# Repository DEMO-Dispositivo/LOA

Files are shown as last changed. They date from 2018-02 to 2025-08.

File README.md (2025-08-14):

# LOA
Robots for Lucifer's Ensemble LOA project.
Playing 3 drums made using Lavacolhos techniques inspired by the Arada drums and other percussions.
The boards are Arduino-based and can receive MIDI through DIN cable or play via SD Card.

## BOARDS

### Legba 
- Arduino MEGA
- 3 servos (5V)
- 7 solenoids (12V)
- 2 motors (5V or 12V)

### Damballah
- Arduino UNO
- 1 servo (5V)
- 3 solenoids (12V)
- 2 motors (5V or 12V)

### Samedi
- Arduino UNO
- 1 servo (5V)
- 3 solenoids (12V)
- 2 motors (5V or 12V)

## BOM
[BOM Spreadsheet](https://docs.google.com/spreadsheets/d/1H9ps_YcNi2U3gRdNnN2o0KlRJA077tAUcP5HMw0Rx48/edit?usp=sharing)

## SCHEMATICS
[Legba board](../master/schematics/Legba_schematic_rev1.pdf)

## MIDI Note Mapping
### Legba
- Note 0: solenoid 1
- Note 2: solenoid 2
- Note 4: solenoid 3
- Note 5: solenoid/motor 4
- Note 7: solenoid/motor 5
- Note/CC 9: servo 1
- Note 36: solenoid 6
- Note 38: solenoid 7 
- Note 40: solenoid 8
- Note/CC 43: servo 2
- Note/CC 45: servo 3

### Damballah
- Note 12: solenoid 1
- Note 14: solenoid 2
- Note 16: solenoid 3
- Note 17: solenoid/motor 4
- Note 19: solenoid/motor 5
- Note 21: servo 1

### Samedi
- Note 24: solenoid 1
- Note 26: solenoid 2
- Note 28: solenoid 3
- Note 29: solenoid/motor 4
- Note 31: solenoid/motor 5
- Note 33: servo 1

## Special thanks to
- Américo Simões
- Tiago Fróis
- Gil MAC and Cláudio Vidal
- FEUP (Faculty of Engineering - University of Porto)
- FCT (Foundation for Science and Technology)

[][cc-by-nc]

This work is licensed under a
[Creative Commons Attribution-NonCommercial 4.0 International License][cc-by-nc].

[][cc-by-nc]

[cc-by-nc]: https://creativecommons.org/licenses/by-nc/4.0/
[cc-by-nc-image]: https://licensebuttons.net/l/by-nc/4.0/88x31.png
[cc-by-nc-shield]: https://img.shields.io/badge/License-CC%20BY--NC%204.0-lightgrey.svg

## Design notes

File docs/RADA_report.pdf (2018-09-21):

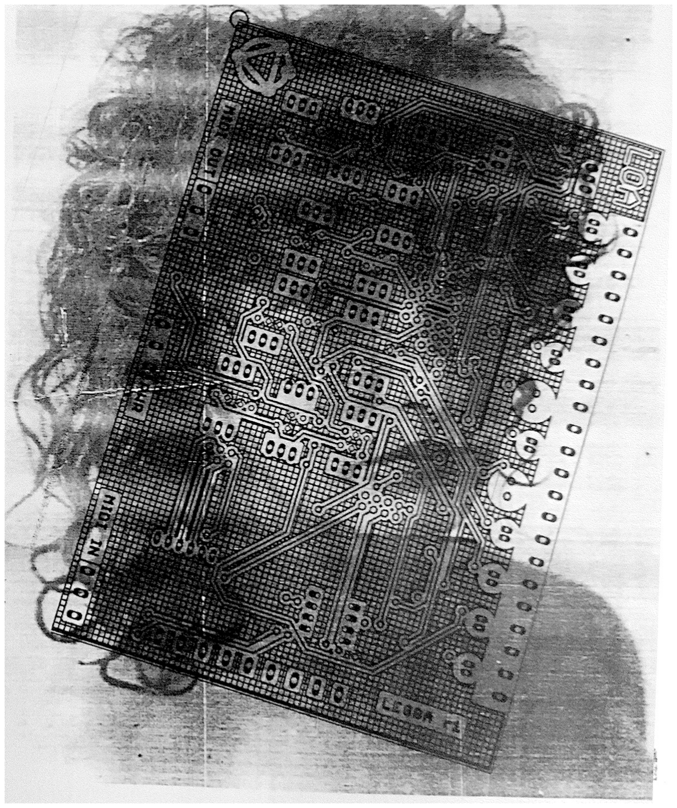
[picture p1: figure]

# RADA™

Tiago Ângelo
FEUP-PDMD
tiago.a.s.angelo@gmail.com
Rada™ | www.tiagoangelo.net

# RESUMO

RADA™ é um ensemble musical robó4co integrado no projecto LOA (https://barosamedi.tumblr.com) desenvolvido pelo colec4vo Lucifer’s Ensemble. (http://www.lucifersensemble.org) Loa é uma reflexão sobre o Vodu do Louisiana e especialmente do Hai4, estabelecendo pontes entre a arte, a antropologia, o experimental e o ancestral. Tendo como ponto de par4da os trabalhos da coreógrafa, bailarina, escritora e cineasta experimental Maya Deren, tais como Religious Possession in Dancing e Divine Horsemen: The Living Gods of Hai4.
Rada refere-se a um conjunto de Loas (divindades) e rituais descendentes do Reino Dahomey (actual República do Benin), cujas cerimónias fazem uso da percussão Rada - um ensemble cons4tuído por uma família de três tambores de madeira com membranas feitas de pele de vaca: o manman (o tambor maior), o segon (tambor médio) e o boula (tambor mais pequeno). Nestas cerimónias a função dos percussionistas é a de es4mular e interagir com a possessão dos par4cipantes, que se mostram ‘montados’ pelos Loas.
O Vodu, como religião ancestral, tem sofrido constantes mutações ao longo dos anos, exibindo diferentes artefactos e expressões culturais mistas espalhadas por diversos países como o Hai4, Benin, Togo, Cuba ou Brasil, para mencionar apenas alguns. Desta forma, o projecto RADA™ não pretende ser uma emulação robó4ca das percussões e percussionistas Rada, mas sim um ensemble robó4co único, inspirado nas suas percussões bem como nos padrões rítmicos usados nos seus vários ritos. Pretendendo explorar a relação entre a música e estados de transe, usando algoritmos de música genera4va para gerar performances de longa duração baseadas em transcrições de um conjunto de padrões musicais dedicados a certos Loas (ex: Legba ou Samedi), colocando a questão: serão os autómatos capazes de nos induzir em estados de transe ?

# ABSTRACT

RADA™ is a robo4c music ensemble integrated in the LOA (https://barosamedi.tumblr.com) project developed by the Lucifer’s Ensemble collec4ve. LOA is a reflec4on over Hai4an and Louisiana Voodoo, bridging art, anthropology, (http://www.lucifersensemble.org) the experimental and the ancestral. The star4ng point of research begins with the works of the choreographer, dancer, writer and experimental filmmaker Maya Deren, such as the Religious Possession in Dancing and Divine Horsemen: The Living Gods of Hai4.
Rada is a set of Loas (dei4es) and rites that descend from the Kingdom of Dahomey (presently Republic of Benin), using in its cerimonies the Rada bacery - an ensemble comprised of a family of three drums made out of carved wood and a membrane made of cowhide: the manman (the biggest drum), segon (medium drum) and boula (smallest drum). Where the drummers role in such rites is to both s4mulate and interact with the possession of the par4cipants, said to be ‘mounted’ by the Loas.
Voodoo, as an ancestral religion, has been under constant muta4on over the ages, exhibi4ng different artefacts and mixed cultural expressions spread around several countries such as Hai4, Benin, Togo, Cuba or Brasil, just to name a few. Likewise, RADA™ is not a robo4c emula4on of the Rada bacery and percussionists but rather a unique robo4c ensemble inspired by Rada drums and the rhythmic pacerns used in its rites. It aims to explore the rela4onship between music and trance states, using genera4ve music algorithms to generate long dura4on performances based on transcrip4ons of a set of musical pacerns dedicated to given Loas (such as Legba or Samedi), posing the ques4on: can automatons induce us into trance-like states ?

# DESCRIÇÃO TÉCNICA

## Instrumentos e actuadores

O ensemble RADA™ é cons4tuído por três tambores construídos por Américo Simões usando as técnicas empregues nos bombos de Lavacolhos (Fundão, Portugal), cujo corpo do instrumento é feito de metal com um aro em madeira, membrana de pele de cabra e corda para es4car/afinar a pele. As dimensões dos tambores são de 50x50cm, 40x40cm e 30x30cm. Para cada tambor existe um controlador responsável por traduzir mensagens MIDI em impulsos eléctricos enviados para os actuadores, sendo que em cada tambor existem:
- 2 motores DC com fitas de tecido que percutem a membrana criando padrões polirrítmicos semi-aleatórios de acordo com a sua velocidade de rotação;
- 3 solenóides com pontas de baqueta construídas para o propósito, percu4ndo a membrana, o aro de madeira e o corpo metálico, respec4vamente;
- 1 servo acoplado a um mecanismo ad hoc que tem a função de pressionar a membrana, criando alterações de tom quando o solenóide percute a membrana.

Os tambores estão suspensos do chão por um suporte em metal desenhado para o propósito, para o qual foram desenhados suportes em madeira que sustentam e posicionam os actuadores de modo a percu4rem os instrumentos.
Adicionalmente poderão exis4r 4 solenóides extra para percu4r vários objectos, à imagem do ogan
- sino usado na percussão Rada - e que de acordo com registos etnográficos poderão ser usados, além de um sino de metal, pedras, garrafas de vidro ou pedaços de espadas de material metálico. Bem como 2 motores servo para cumprir a função do ason (maraca). Estes controlos fazem parte do controlador LEGBA, correspondente ao tambor maior.

## Controladores e configuração

De modo a controlar todos os actuadores existem 3 caixas (LEGBA, DAMBALLAH e SAMEDI) contendo um Arduino¹, uma fonte de alimentação comutada de 12V, uma fonte de alimentação comutada de 5V, uma PCB 4po shield de Arduino para controlo dos actuadores bem como envio e recepção de mensagens MIDI. Cada caixa inclui ligações de corrente eléctrica com conector Speakon, entrada e saída MIDI via XLR, entrada DC para alimentação do Arduino, porta USB para programação, saídas DC para conexão de motores e solenóides e saídas Jack stereo 6.3mm para conexão dos servos.
O controlo do autómato (ver figura em baixo) é realizado através de um computador ligado a uma interface MIDI que por sua vez se liga ao controlador LEGBA usando um cabo conversor de MIDI DIN (5 pinos a 180°) para XLR, que por sua vez transmite as mensagens MIDI através de cabos XLR ligados em série aos restantes controladores.

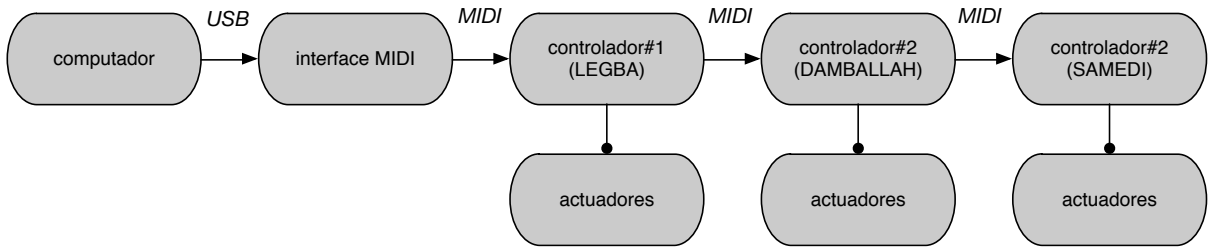
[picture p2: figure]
computador; interface MIDI; controlador#1; (LEGBA); controlador#2 (DAMBALLAH); controlador#2 (SAMEDI); actuadores; USB; MIDI

1 www.arduino.cc

## Composição generaDva em tempo-real

O algoritmo responsável pela execução do autómato é cons4tuído por três fases dis4ntas (ver fig. em baixo):
1. Transcrição e colecção: numa primeira fase será feita uma transcrição manual de vários registos² em formato áudio ou par4tura de música tradicional do Hai4, procedendo-se a uma codificação para um formato próprio para o posterior algoritmo gené4co e gravação destes ficheiros codificados numa base de dados;
2. Nesta fase proceder-se-á à geração de vários ficheiros codificados de modo a treinar uma rede neuronal supervisionada de modo a que na fase seguinte a função de fitness (fitness func6on) seja automá4ca (sem supervisão), escolhendo as ‘melhores’ gerações de padrões musicais.
3. A úl4ma fase será a que ficará em funcionamento durante a instalação, sendo que o algoritmo irá correr de modo conxnuo desde o início ao final do fes4val Semibreve (mesmo que se reinicie o sistema diariamente). Nesta fase o algoritmo irá inicialmente começar a gerar padrões musicais recorrendo à base de dados inicial (ficheiros codificados de música tradicional hai4ana) sendo a piscina gené4ca (gene6c pool) retro-alimentada com novas gerações que passem no função de fitness. Este processo fará com que inicialmente a instalação comece com padrões musicais com elevado grau de semelhança em relação às transcrições iniciais e caminhe progressivamente para o ‘desconhecido’, isto é, poderá terminar com padrões musicais completamente diferentes dos iniciais, sendo introduzidas ligeiras mutações gené4cas nos padrões a cada iteração.

Base de
dados
inicial

Partituras ou
gravações áudio

Ficheiro
codificado

Transcrição
manual | Codificação

### Fase 1: transcrição e colecção

### Fase 2: treino

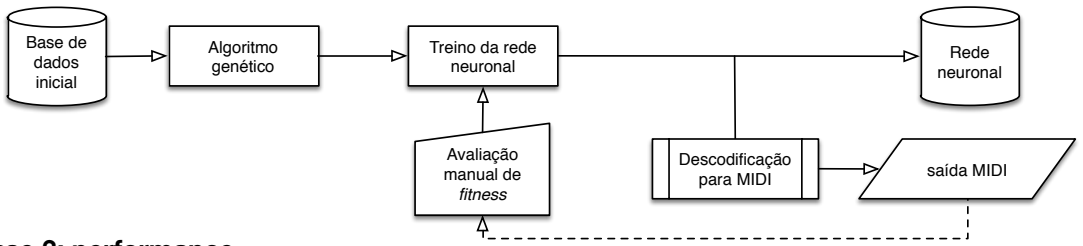
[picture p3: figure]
Rede neuronal; Base de dados inicial; Algoritmo genético; Treino da rede neuronal; Avaliação manual de fitness; saída MIDI Descodificação para MIDI

### Fase 3: performance

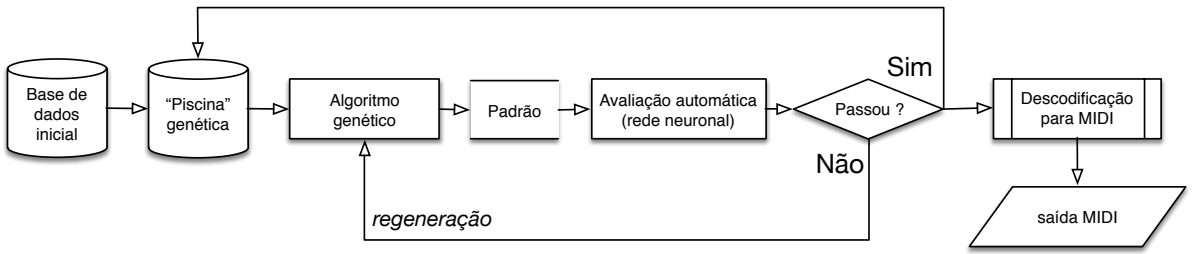
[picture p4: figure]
“Piscina” genética; Base de dados inicial; Algoritmo genético; Avaliação automática; (rede neuronal) Padrão; Passou ?; Sim; Não; regeneração; Descodificação para MIDI; saída MIDI

2 Fontes principais: “The Drum and the Hoe: Life and Lore of the Hai4an People” (Harold Courlander, 1960); “Voodoo Trance Music Ritual Drums of Hai4” (Lyrichord edi4on, 1974); “Divine Horsemen - The Voodoo Gods of Hai4” (recorded by Maya Deren, 1947-51, Lyrichord edi4on)

# PLANO DE MONTAGEM

1. Colocação das bases metálicas
2. Colocação dos tambores nas bases metálicas
3. Colocação dos suportes de madeira
4. Colocação do suporte lateral de acordo com a marcação (LEGBA no tambor grande, DAMBALLAH no médio e SAMEDI no pequeno)
5. Colocação das caixas ao lado de cada tambor: caixa LEGBA com o tambor maior, caixa DAMBALLAH com o tambor médio, caixa SAMEDI com o tambor pequeno
6. Ligação dos cabos dos actuadores de cada tambor à respec4va caixa de acordo com a enumeração marcada no cabo e na caixa
7. Ligação dos 2 cabos XLR (LEGBA MIDI OUT —> DAMBALLAH MIDI IN e DAMBALLAH MIDI OUT —> Samedi MIDI IN)
8. Ligação de corrente: 3 cabos Speakon e 3 adaptadores 12V DC providenciados
9. Ligação da interface MIDI ao computador conectando o cabo conversor (DIN-XLR) ao MIDI OUTPUT da interface, usando um cabo XLR rela4vamente comprido para fazer a conexão entre o cabo conversor e a caixa LEGBA na ficha MIDI IN
10. Ligar o computador (que deverá arrancar automa4camente o programa RADA). Pressionar a tecla ’T’ do teclado do computador para testar e pressionar a tecla ‘ENTER’ para começar. No caso de engano poder-se-á pressionar a tecla ‘C’ para restabelecer o programa ao estado inicial, pressionando novamente a tecla ‘ENTER’ para começar.
11. Depois poder-se-á desconectar o teclado do computador e guardar, ficando apenas o monitor visível para efeitos de visualização da geração de padrões musicais.
12. Colocação de pufes ou lugares sentados para escuta.

Duração prevista de montagem: 4h; 2 pessoas; material necessário: chave inglesa e alicate de pontas.

## Disposição:

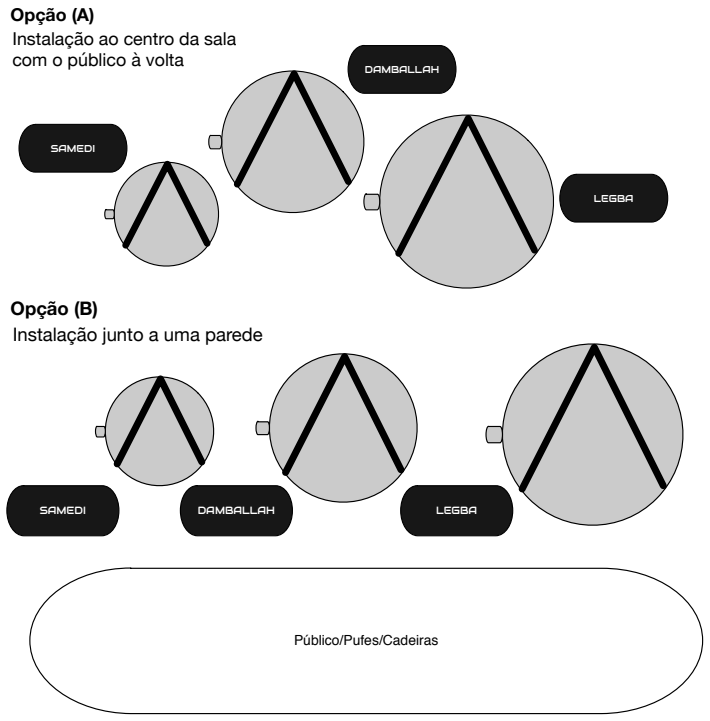
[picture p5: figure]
Opção (A); LEGBA; DAMBALLAH; SAMEDI; Instalação ao centro da sala com o público à volta; Opção (B); Instalação junto a uma parede; Público/Pufes/Cadeiras

## Raider:

1. Computador
2. Extensão de corrente eléctrica para 12 tomadas
3. [OPCIONAL] PA, mesa de mistura e 3 microfones com tripé de chão para amplificação dos tambores, dependendo da localização da instalação e acús4ca da sala (a combinar com o autor)

## Notas:

- O computador deverá ser programado para iniciar e terminar automa4camente para poder gravar a piscina gené4ca automa4camente de modo a poder con4nuar do mesmo sí4o no dia seguinte. Para tal é necessário que haja corrente eléctrica a uma determinada hora (a combinar com a ins4tuição de acolhimento) e que se desligue apenas depois do computador se ter desligado automa4camente. Para tal terá que se instalar um script no computador.
- O computador poderá ter sistema opera4vo Windows ou OSX. A versão é indiferente desde que conhecida previamente para efeitos de testes, embora seja preferido o sistema opera4vo OSX entre 10.9 e 10.11. A interface MIDI poderá no entanto ser providenciada pelo autor.

# Créditos

Tiago Ângelo - conceito, electrónica, programação e composição. Tiago Fróis - desenho e construção de suportes mecânicos. Américo Simões - construção dos tambores.

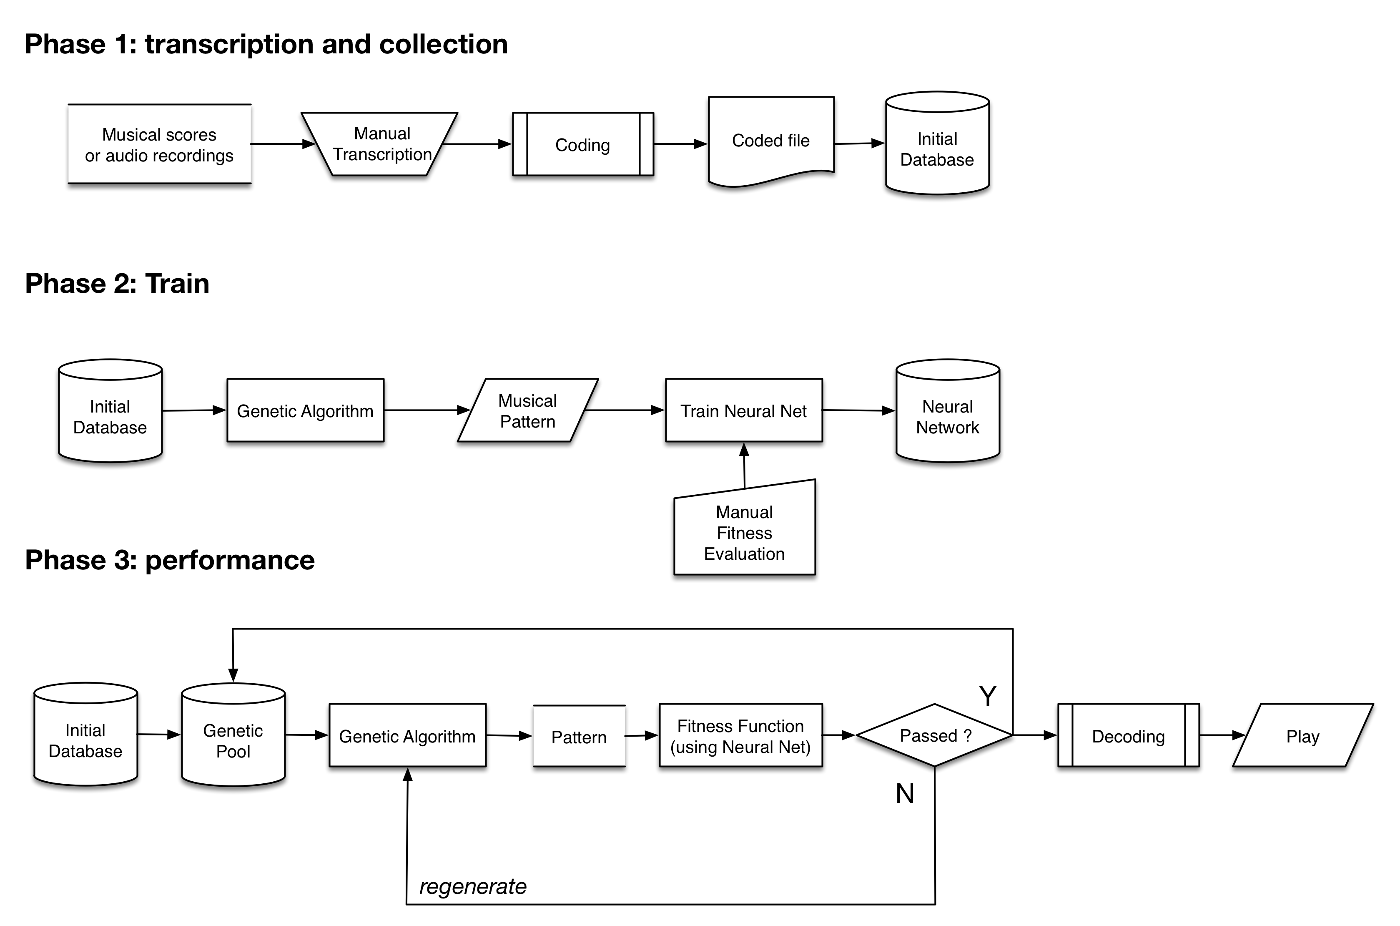
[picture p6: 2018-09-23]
MaxMSP/media/general_diagram.png

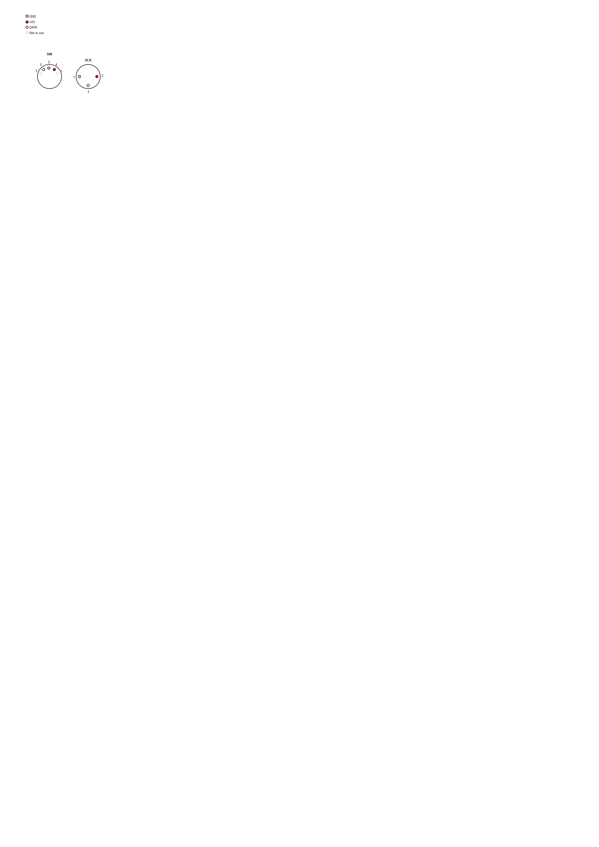
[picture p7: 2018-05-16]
docs/DIN to XLR.png

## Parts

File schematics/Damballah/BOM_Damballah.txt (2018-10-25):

Partlist exported from C:/Users/tiago/Documents/GitHub/LOA/schematics/Damballah/LOA_Damballah.sch at 25-09-2018 17:31

Qty Value               Device              Package            Parts                                                 Description                          
1                       FE06W               FE06W              SV1                                                   FEMALE HEADER                        
11                      W237-102            W237-102           L1, L2, L3, L4, L5, L6, L7, L8, L9, M4, M5            WAGO SCREW CLAMP                     
6                       W237-103            W237-103           MIDI_IN, MIDI_OUT, PWRIN, S1, S2, S3                  WAGO SCREW CLAMP                     
11  0.1uF               CNP-C025-050X025    C025-050X025       C13, C15, C17, C19, C21, C23, C25, C27, C29, C31, C33 NON-POLARIZED CAP                    
11  0.22uF              CNP-C025-050X025    C025-050X025       C12, C14, C16, C18, C20, C22, C24, C26, C28, C30, C32 NON-POLARIZED CAP                    
9   100uF               CPOL-USE3.5-8       E3,5-8             C1, C2, C3, C4, C5, C6, C7, C8, C9                    POLARIZED CAPACITOR, American symbol 
11  1A/50V/1.1V         DIODE-KIT2          DIODE-1N4001-KIT   D1, D2, D3, D4, D5, D6, D7, D8, D9, D10, D11          Diode                                
11  1k                  1KOHM-VERT-1/4W-1%  AXIAL-0.1          R1, R2, R3, R4, R5, R6, R7, R8, R9, R10, R11          1kO resistor                         
1   200mA/100V/1V       DIODE-1N4148        DIODE-1N4148       D12                                                   Diode                                
3   220                 1KOHM-HORIZ-1/4W-5% AXIAL-0.3          R12, R13, R15                                         1kO resistor                         
2   220uF               CP-E-035X080        E-035X080          C10, C11                                              POLARIZED CAP                        
1   4K7                 1KOHM-HORIZ-1/4W-5% AXIAL-0.3          R14                                                   1kO resistor                         
1   6N138               6N138               DIL08              OK1                                                   MOTOROLA OPTO COUPLER                
2   7806                78XXS               78XXS              IC10, IC11                                            VOLTAGE REGULATOR                    
9   7815                78XXS               78XXS              IC1, IC2, IC3, IC4, IC5, IC6, IC7, IC8, IC9           VOLTAGE REGULATOR                    
1   ARDUINO_MEGA_R3FULL ARDUINO_MEGA_R3FULL ARDUINO_MEGA       B1                                                    Arduino Mega R3                      
2   IRF510              IRF520              TO220BV            Q10, Q11                                              HEXFET Power MOSFET                  
9   TIP120              ROCKETFARM_TIP120V  ROCKETFARM_TO220AV Q1, Q2, Q3, Q4, Q5, Q6, Q7, Q8, Q9                    NPN DARLINGTON TRANSISTOR

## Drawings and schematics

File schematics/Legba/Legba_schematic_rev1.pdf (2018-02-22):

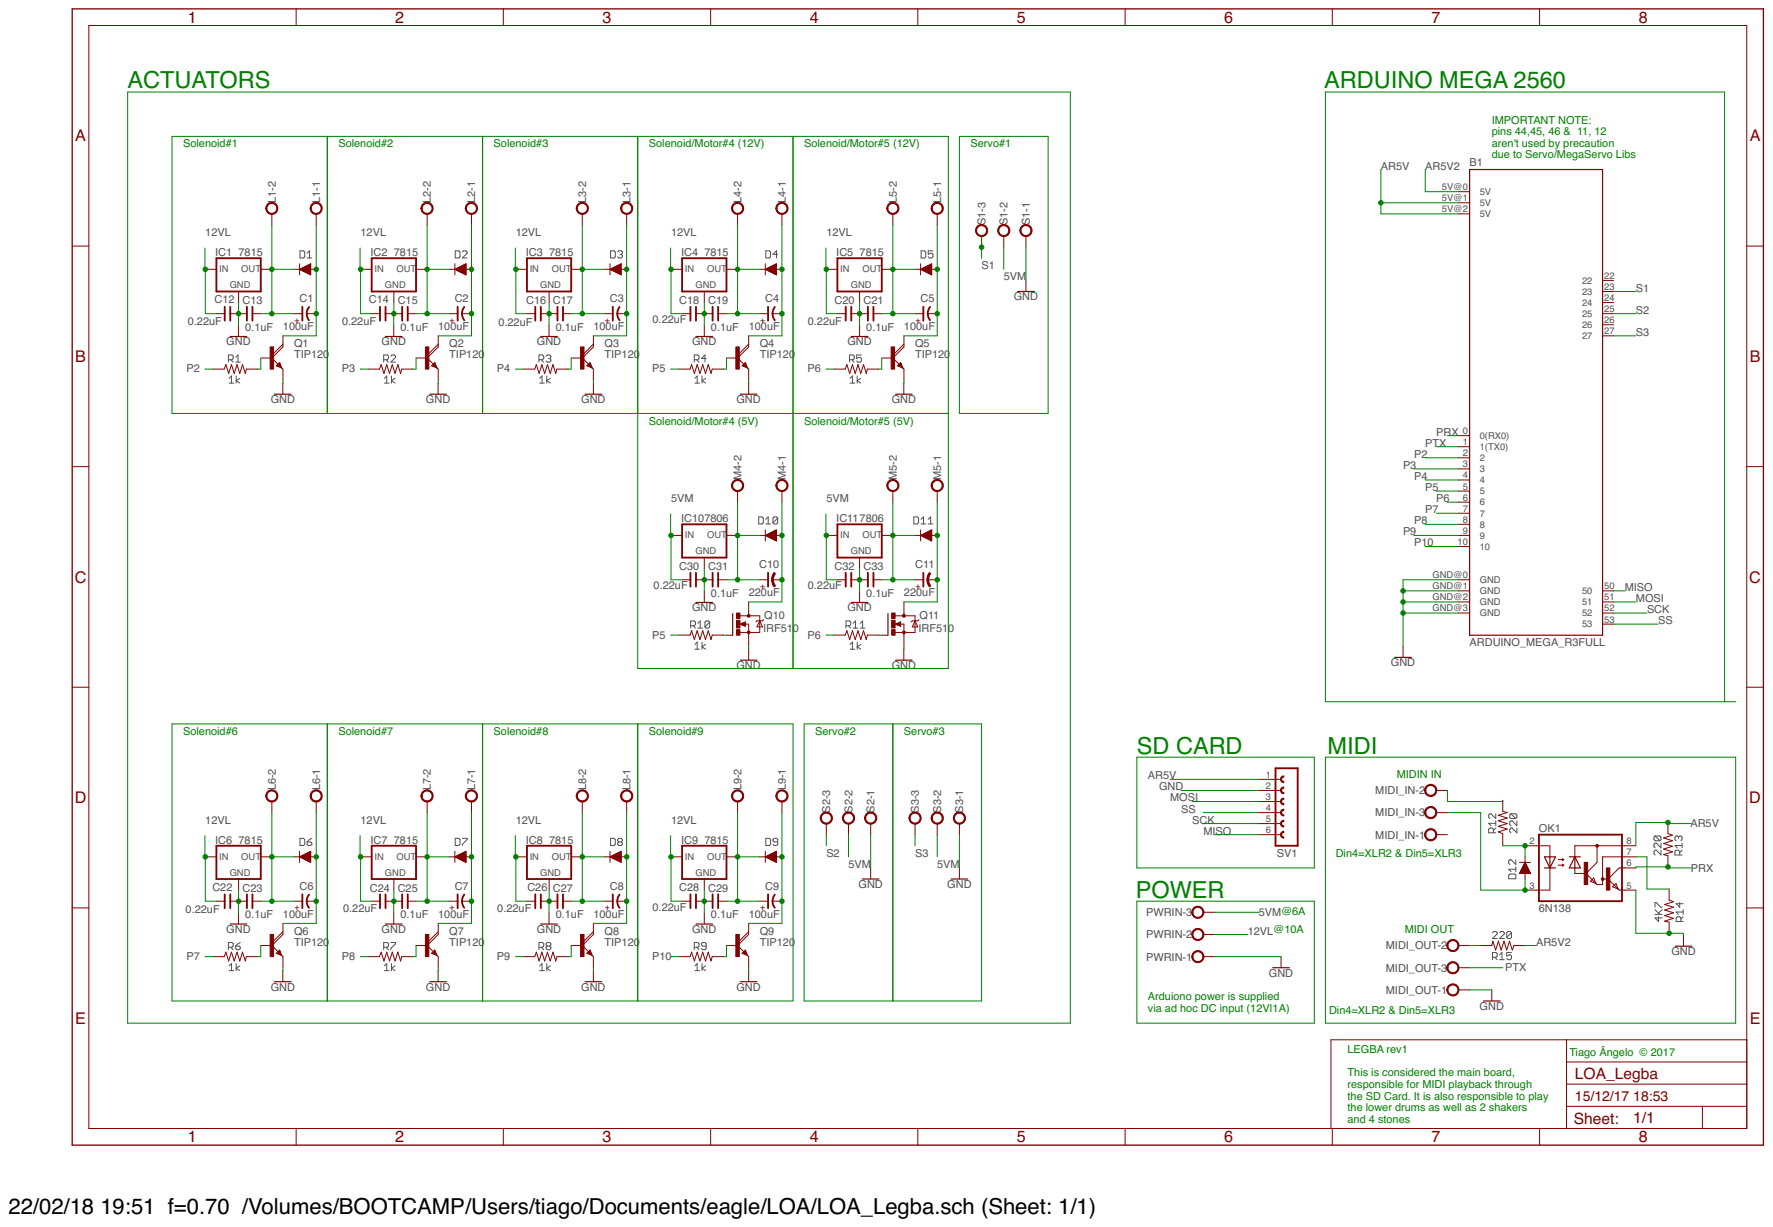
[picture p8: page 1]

aren't used by precaution

PWRIN-1 PWRIN-2 PWRIN-3 5VM @10A @6A 12VL Arduiono power is supplied via ad hoc DC input (12V|1A)

MIDI_OUT-1 MIDI_OUT-2 MIDI_OUT-3

LEGBA rev1 This is considered the main board, responsible for MIDI playback through

the SD Card. It is also responsible to play
the lower drums as well as 2 shakers and 4 stones

22/02/18 19:51 f=0.70 /Volumes/BOOTCAMP/Users/tiago/Documents/eagle/LOA/LOA_Legba.sch (Sheet: 1/1)

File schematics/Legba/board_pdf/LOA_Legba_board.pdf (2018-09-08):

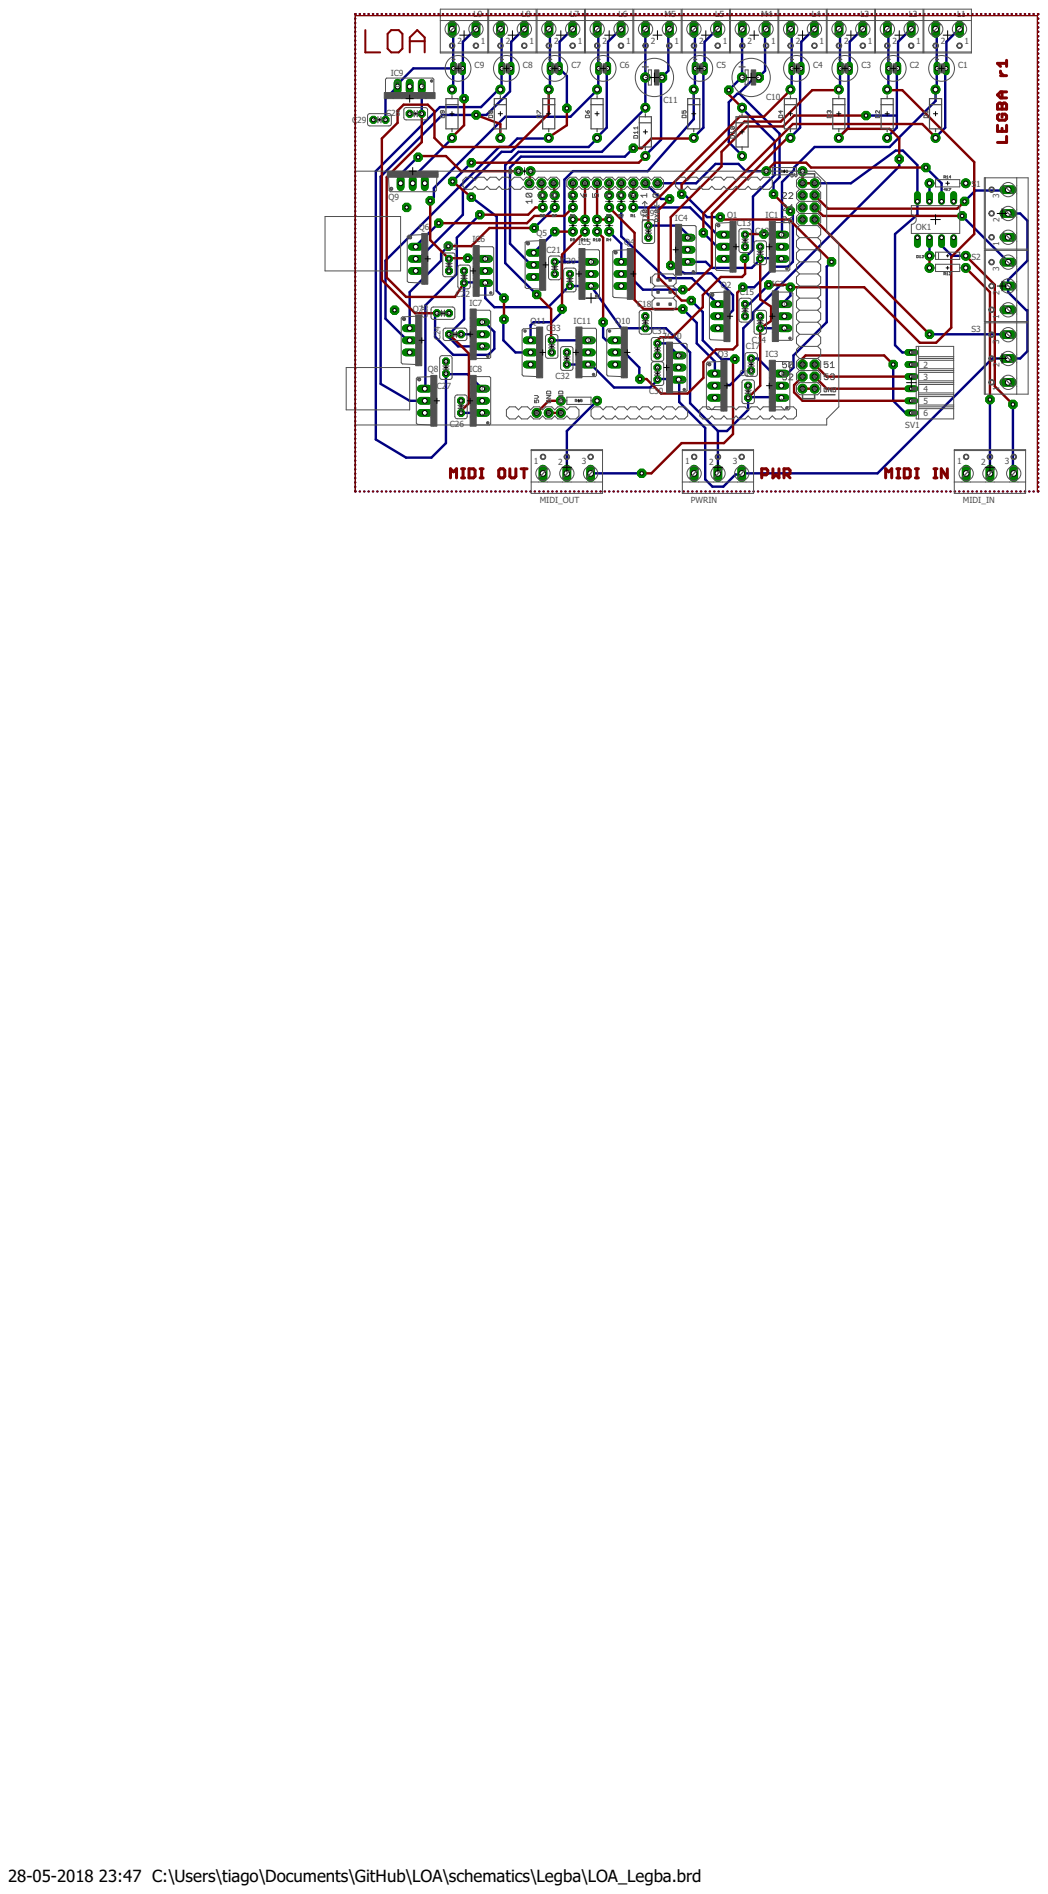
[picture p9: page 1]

28-05-2018 23:47 C:\Users\tiago\Documents\GitHub\LOA\schematics\Legba\LOA_Legba.brd

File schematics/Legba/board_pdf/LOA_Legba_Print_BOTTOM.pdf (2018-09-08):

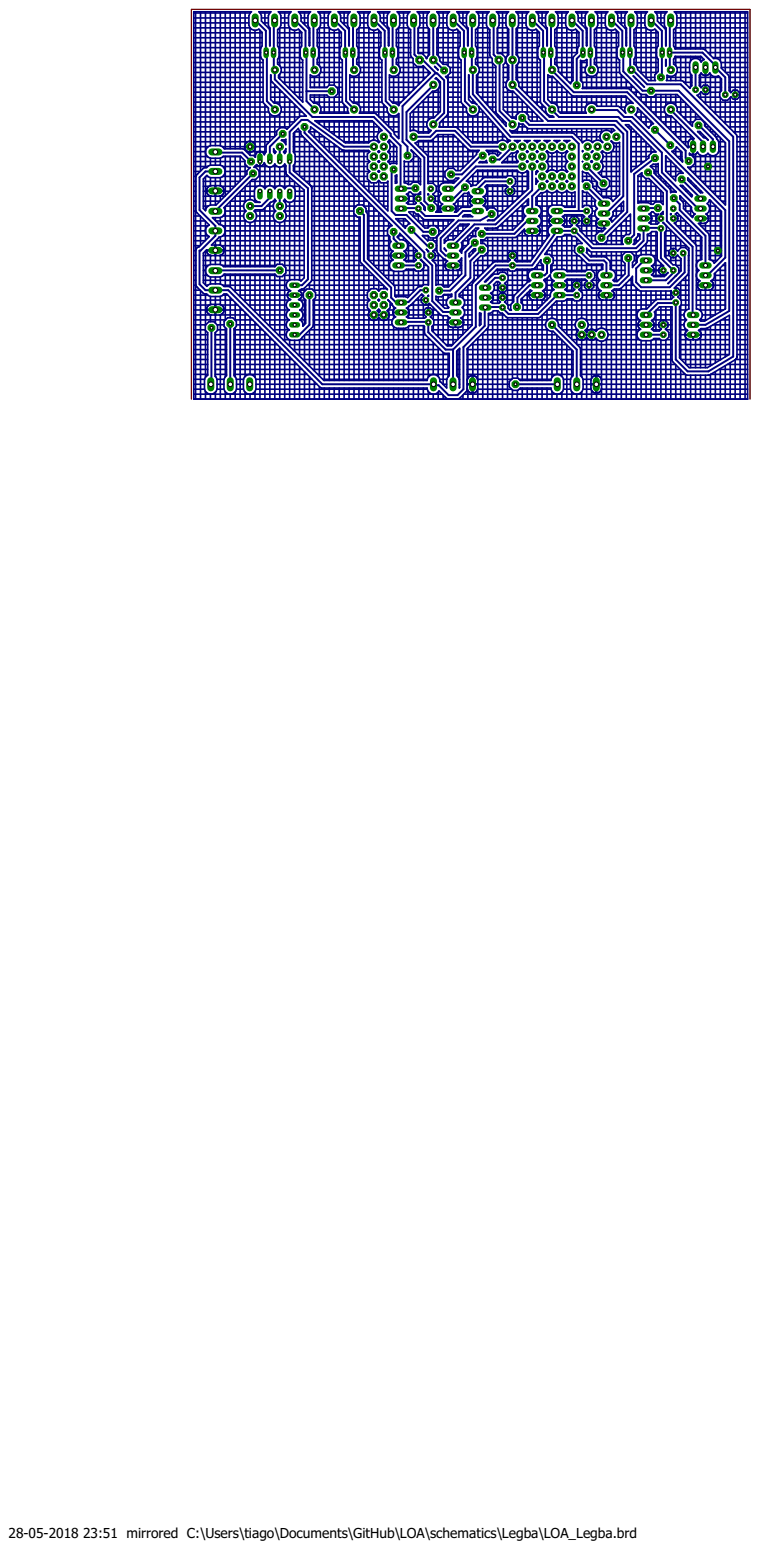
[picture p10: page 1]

28-05-2018 23:51 mirrored C:\Users\tiago\Documents\GitHub\LOA\schematics\Legba\LOA_Legba.brd

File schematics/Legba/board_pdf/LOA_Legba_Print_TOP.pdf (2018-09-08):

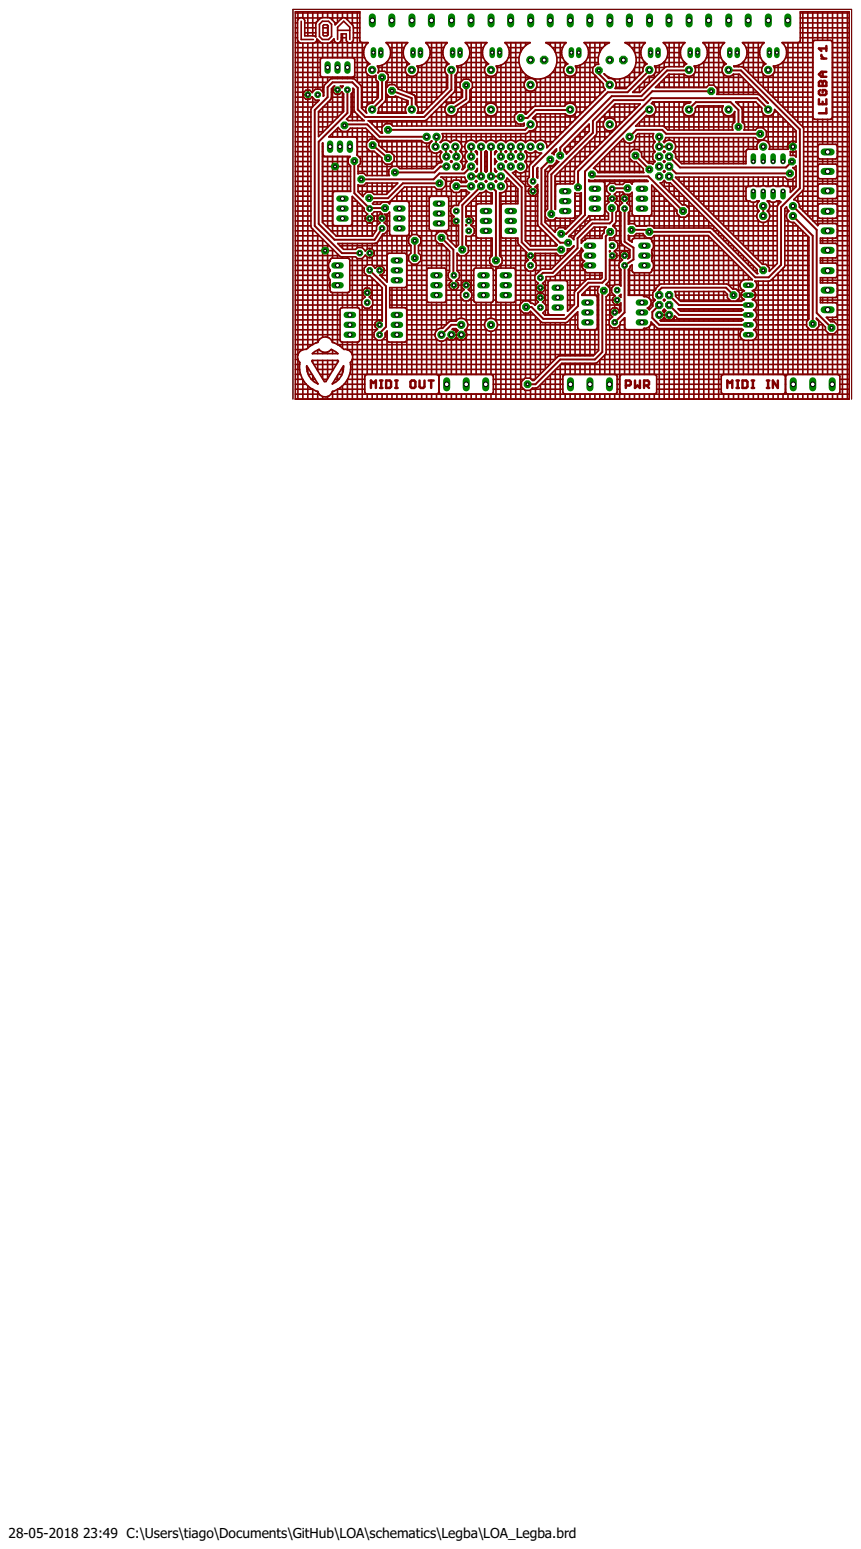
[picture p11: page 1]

28-05-2018 23:49 C:\Users\tiago\Documents\GitHub\LOA\schematics\Legba\LOA_Legba.brd

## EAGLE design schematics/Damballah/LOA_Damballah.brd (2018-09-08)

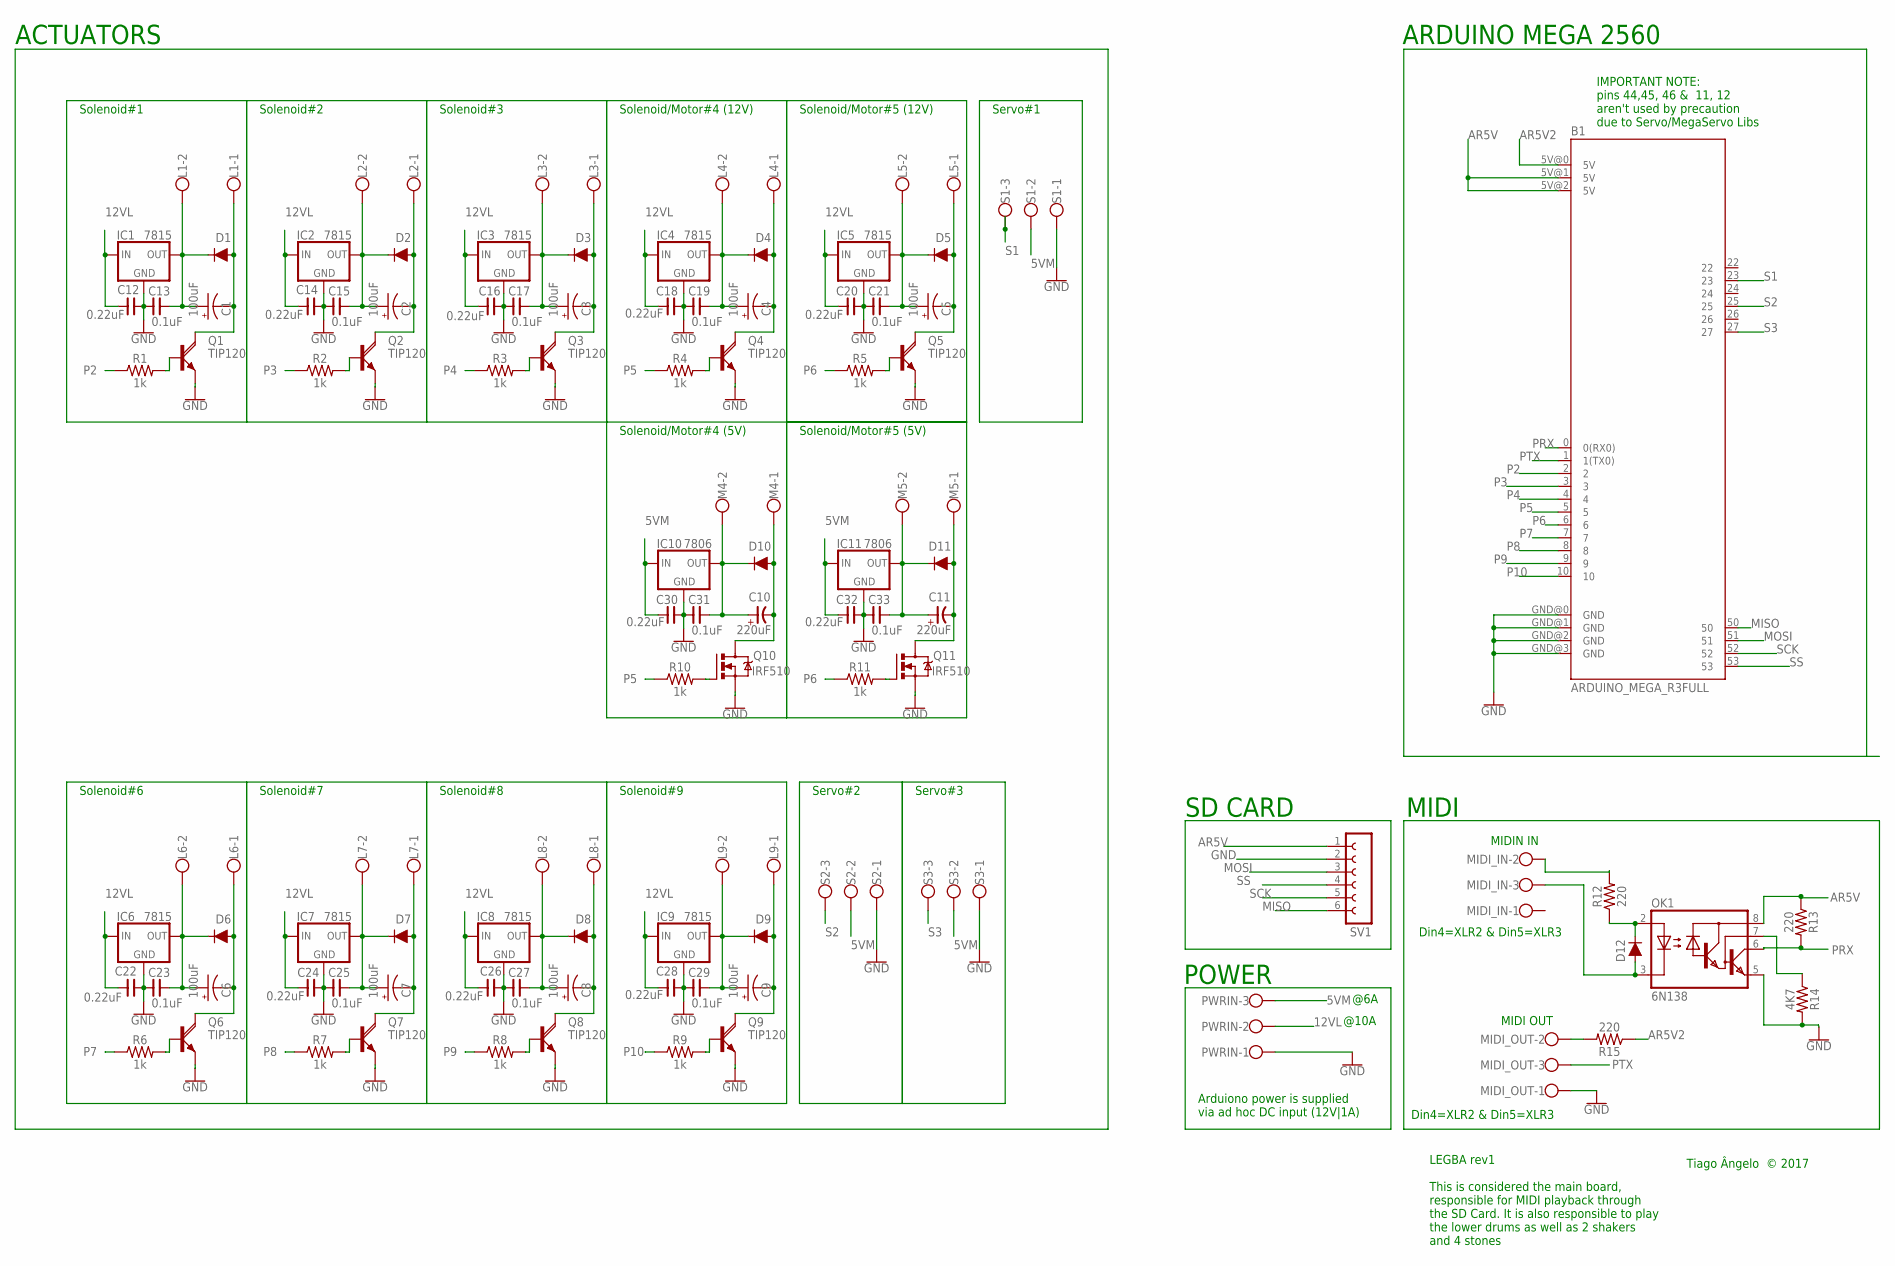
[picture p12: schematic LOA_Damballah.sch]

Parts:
B1: ARDUINO_MEGA_R3FULL; ARDUINO_MEGA
C1, C2, C3, C4, C5, C6, C7, C8, C9: 100uF; E3,5-8
C10, C11: 220uF; E-035X080
C12, C14, C16, C18, C20, C22, C24, C26, C28, C30, C32: 0.22uF; C025-050X025
C13, C15, C17, C19, C21, C23, C25, C27, C29, C31, C33: 0.1uF; C025-050X025
D1, D2, D3, D4, D5, D6, D7, D8, D9, D10, D11: 1A/50V/1.1V; DIODE-1N4001-KIT
D12: 200mA/100V/1V; DIODE-1N4148
IC1, IC2, IC3, IC4, IC5, IC6, IC7, IC8, IC9: 7815; 78XXS
IC10, IC11: 7806; 78XXS
L1, L2, L3, L4, L5, L6, L7, L8, L9: W237-102
M4, M5: W237-102
MIDI_IN: W237-103
MIDI_OUT: W237-103
OK1: 6N138; DIL08
PWRIN: W237-103
Q1, Q2, Q3, Q4, Q5, Q6, Q7, Q8, Q9: TIP120; ROCKETFARM_TO220AV
Q10, Q11: IRF510; TO220BV
R1, R2, R3, R4, R5, R6, R7, R8, R9, R10, R11: 1k; AXIAL-0.1
R12, R13, R15: 220; AXIAL-0.3
R14: 4K7; AXIAL-0.3
S1, S2, S3: W237-103
SV1: FE06W

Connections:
5VM: C30.1, C32.1, IC10.IN, IC11.IN, PWRIN.3, S1.2, S2.2, S3.2
12VL: C12.1, C14.1, C16.1, C18.1, C20.1, C22.1, C24.1, C26.1, C28.1, IC1.IN, IC2.IN, IC3.IN, IC4.IN, IC5.IN, IC6.IN, IC7.IN, IC8.IN, IC9.IN, PWRIN.2
AR5V: B1.5V@1 (5V), B1.5V@2 (5V), OK1.8 (VCC), R13.P$1 (1), SV1.1
AR5V2: B1.5V@0 (5V), R15.P$1 (1)
GND: B1.GND@0 (GND), B1.GND@1 (GND), B1.GND@2 (GND), B1.GND@3 (GND), C12.2, C13.1, C14.2, C15.1, C16.2, C17.1, C18.2, C19.1, C20.2, C21.1, C22.2, C23.1, C24.2, C25.1, C26.2, C27.1, C28.2, C29.1, C30.2, C31.1, C32.2, C33.1, IC1.GND, IC2.GND, IC3.GND, IC4.GND, IC5.GND, IC6.GND, IC7.GND, IC8.GND, IC9.GND, IC10.GND, IC11.GND, MIDI_OUT.1, OK1.5 (GND), PWRIN.1, Q1.E, Q2.E, Q3.E, Q4.E, Q5.E, Q6.E, Q7.E, Q8.E, Q9.E, Q10.S, Q11.S, R14.P$2 (2), S1.1, S2.1, S3.1, SV1.2
L1-1: C1.-, D1.A, L1.1, Q1.C
L1-2: C1.+, C13.2, D1.C, IC1.OUT, L1.2
L2-1: C2.-, D2.A, L2.1, Q2.C
L2-2: C2.+, C15.2, D2.C, IC2.OUT, L2.2
L3-1: C3.-, D3.A, L3.1, Q3.C
L3-2: C3.+, C17.2, D3.C, IC3.OUT, L3.2
L4-1: C4.-, D4.A, L4.1, Q4.C
L4-2: C4.+, C19.2, D4.C, IC4.OUT, L4.2
L5-1: C5.-, D5.A, L5.1, Q5.C
L5-2: C5.+, C21.2, D5.C, IC5.OUT, L5.2
L6-1: C6.-, D6.A, L6.1, Q6.C
L6-2: C6.+, C23.2, D6.C, IC6.OUT, L6.2
L7-1: C7.-, D7.A, L7.1, Q7.C
L7-2: C7.+, C25.2, D7.C, IC7.OUT, L7.2
L8-1: C8.-, D8.A, L8.1, Q8.C
L8-2: C8.+, C27.2, D8.C, IC8.OUT, L8.2
L9-1: C9.-, D9.A, L9.1, Q9.C
L9-2: C9.+, C29.2, D9.C, IC9.OUT, L9.2
M4-1: C10.-, D10.A, M4.1, Q10.D
M4-2: C10.+, C31.2, D10.C, IC10.OUT, M4.2
M5-1: C11.-, D11.A, M5.1, Q11.D
M5-2: C11.+, C33.2, D11.C, IC11.OUT, M5.2
MISO: B1.50, SV1.6
MOSI: B1.51, SV1.3
unnamed: Q10.G, R10.P$2 (2)
unnamed: MIDI_OUT.2, R15.P$2 (2)
unnamed: Q2.B, R2.P$2 (2)
unnamed: Q3.B, R3.P$2 (2)
unnamed: Q4.B, R4.P$2 (2)
unnamed: Q5.B, R5.P$2 (2)
unnamed: Q11.G, R11.P$2 (2)
unnamed: Q6.B, R6.P$2 (2)
unnamed: Q7.B, R7.P$2 (2)
unnamed: Q8.B, R8.P$2 (2)
unnamed: Q1.B, R1.P$2 (2)
unnamed: Q9.B, R9.P$2 (2)
unnamed: D12.A, MIDI_IN.3, OK1.3 (C)
unnamed: D12.C, OK1.2 (A), R12.P$1 (1)
unnamed: MIDI_IN.2, R12.P$2 (2)
unnamed: OK1.7 (VB), R14.P$1 (1)
P2: B1.2, R1.P$1 (1)
P3: B1.3, R2.P$1 (1)
P4: B1.4, R3.P$1 (1)
P5: B1.5, R4.P$1 (1), R10.P$1 (1)
P6: B1.6, R5.P$1 (1), R11.P$1 (1)
P7: B1.7, R6.P$1 (1)
P8: B1.8, R7.P$1 (1)
P9: B1.9, R8.P$1 (1)
P10: B1.10, R9.P$1 (1)
PRX: B1.0 (0(RX0)), OK1.6 (VO), R13.P$2 (2)
PTX: B1.1 (1(TX0)), MIDI_OUT.3
S1: B1.23, S1.3
S2: B1.25, S2.3
S3: B1.27, S3.3
SCK: B1.52, SV1.5
SS: B1.53, SV1.4

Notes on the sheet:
Tiago Ângelo © 2017
Din4=XLR2 & Din5=XLR3
MIDI OUT
MIDIN IN
MIDI
POWER
Arduiono power is supplied via ad hoc DC input (12V|1A)
IMPORTANT NOTE: pins 44,45, 46 & 11, 12 aren't used by precaution due to Servo/MegaServo Libs
Solenoid#1
Solenoid#2
Solenoid#3
Servo#1
Solenoid/Motor#4 (5V)
Solenoid/Motor#5 (5V)
Solenoid/Motor#4 (12V)
Solenoid/Motor#5 (12V)
Servo#2
Servo#3
Solenoid#6
Solenoid#7
Solenoid#8
Solenoid#9
SD CARD
ARDUINO MEGA 2560
ACTUATORS
@10A
@6A
LEGBA rev1 This is considered the main board, responsible for MIDI playback through the SD Card. It is also responsible to play the lower drums as well as 2 shakers and 4 stones

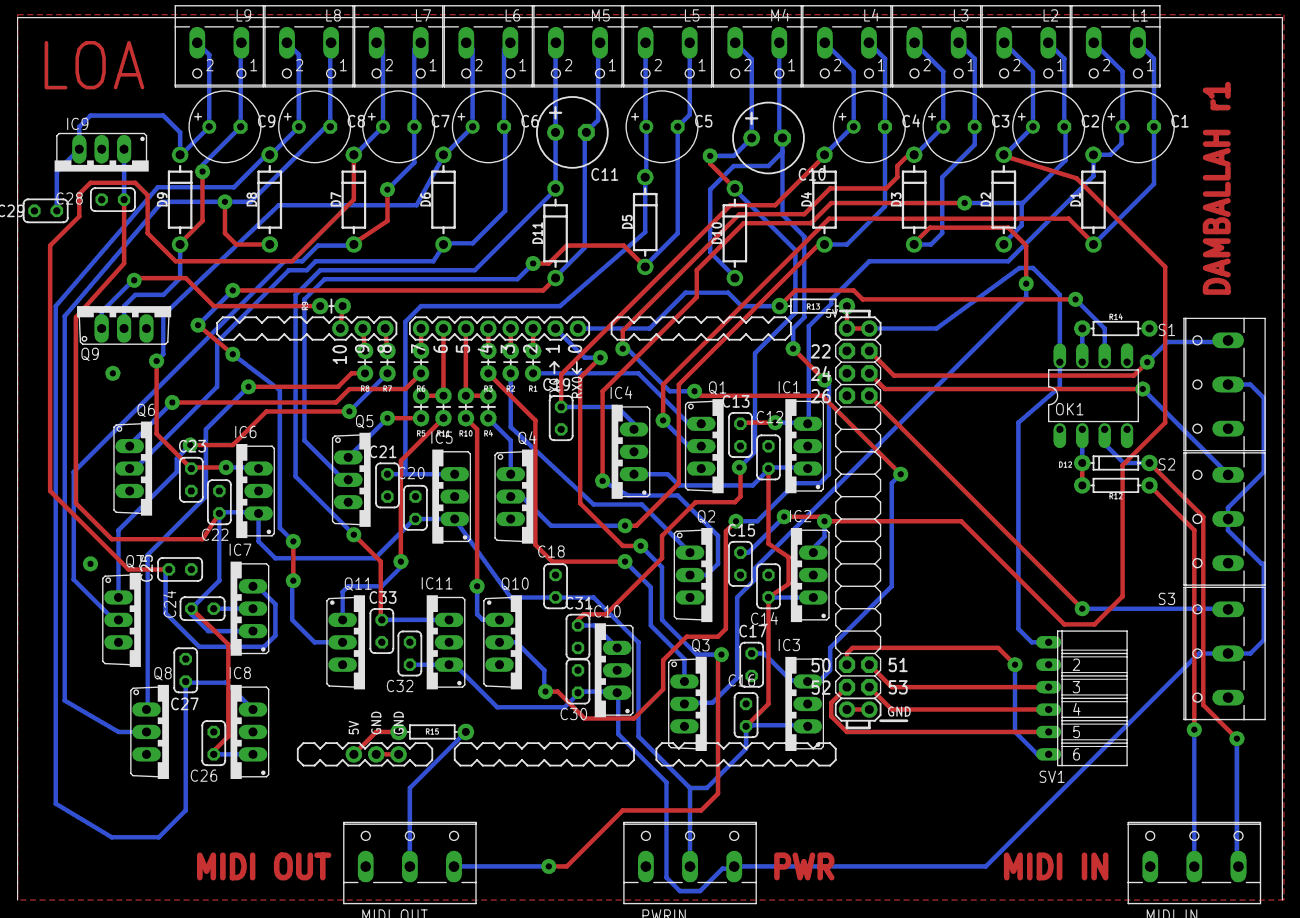
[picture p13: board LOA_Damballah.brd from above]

Board: 2 copper layers, 143.3 x 100.0 mm, 102 parts (0 on the bottom side), 61 nets.

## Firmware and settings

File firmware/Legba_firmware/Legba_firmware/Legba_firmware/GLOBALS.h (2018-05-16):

/*
 * GLOBALS.h
 *
 * Created: 01-05-2018 21:09:29
 *  Author: tiago
 */ 

#ifndef GLOBALS_H_
#define GLOBALS_H_

#define LED 13
#define MIDICH 13

/*#define STARTNOTE_A 0
#define STARTNOTE_B 36
#define SERVOS 3
#define NOTES_A 12
#define NOTES_B 12
*/

// MOTORS PINS
#define M4 5 // note 5
#define M5 6 // note 7
// SOLENOIDS PINS
#define L1 2 // note 0
#define L2 3 // note 2
#define L3 4 // note 4
#define L6 7 // note 36
#define L7 8 // note 38
#define L8 9 // note 40
#define L9 10 // note 41


// SERVOS' PINS
#define S1 23 // note/cc 9
#define S1CC 9
#define S2 25 // note/cc 43
#define S2CC 43
#define S3 27 // note/cc 45
#define S3CC 45

/* Addresses on Arduino EEPROM for servo control parameters*/
#define S1MINANG 0 // servo1 min angle (cc=122)
#define S1MAXANG 1 // servo1 max angle (cc=123)

#define S2MINANG 2 // servo2 min angle (cc=124)
#define S2MAXANG 3 // servo2 max angle (cc=125)

#define S3MINANG 4 // servo3 min angle (cc=126)
#define S3MAXANG 5 // servo3 max angle (cc=127)

#endif /* GLOBALS_H_ */

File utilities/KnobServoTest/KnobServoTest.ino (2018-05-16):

/* test servo */

#include <Servo.h>

Servo myservo;  // create servo object to control a servo

void setup() {
  Serial.begin(9600);
  myservo.attach(9);  // attaches the servo on pin 9 to the servo object
}

void loop() {
  if(Serial.available()){
    byte val = Serial.parseInt();
    myservo.write( 180-val );
    Serial.println(val);
  }
}

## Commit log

2018-02-22 added BOM
2018-02-22 added schematic for Legba board
2018-04-30 added schematics for Legba board
    [LOA_Legba.brd, LOA_Legba.sch]
2018-04-30 added 1st firmware sketch
    (copied from Phobos board #7)
2018-05-28 updated servo controller
    added control for damballah and samedi
2018-09-08 Uploaded samedi board
    Samedi and Damballah are prepared to handle 24V solenoids
    (the only difference in the etch to Legba is the 100uF caps)
    [LOA_Samedi.brd, LOA_Samedi.sch]
2018-09-08 minor change
    [LOA_Samedi.brd]
2018-09-08 uploaded Damballah board
    [LOA_Damballah.brd, LOA_Damballah.sch]
2018-09-25 uploaded BOM's

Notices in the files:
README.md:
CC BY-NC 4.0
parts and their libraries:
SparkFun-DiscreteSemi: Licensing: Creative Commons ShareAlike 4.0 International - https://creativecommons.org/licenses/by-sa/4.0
